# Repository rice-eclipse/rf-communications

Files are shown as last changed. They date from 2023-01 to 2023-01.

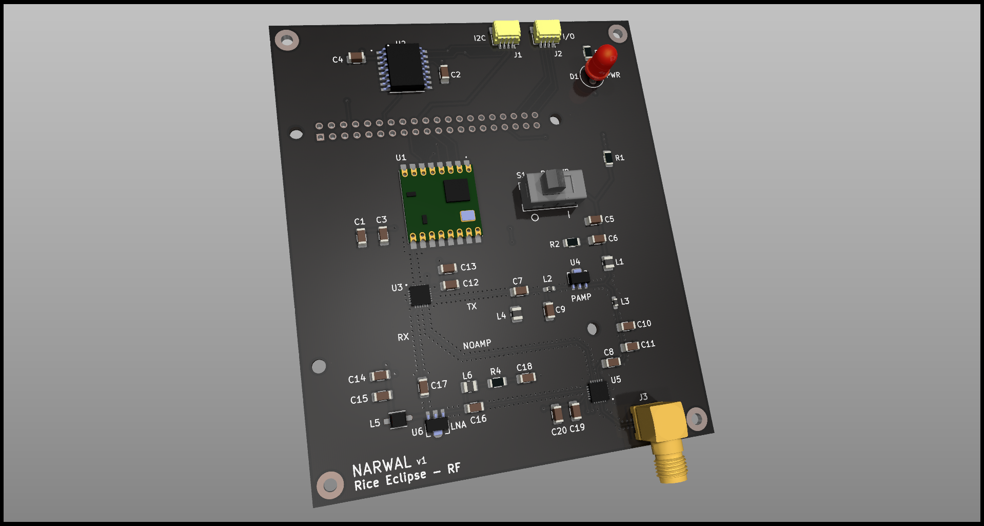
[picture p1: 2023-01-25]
narwal/Narwal_v1/Screenshots/Narwal_side_pop_ray.png

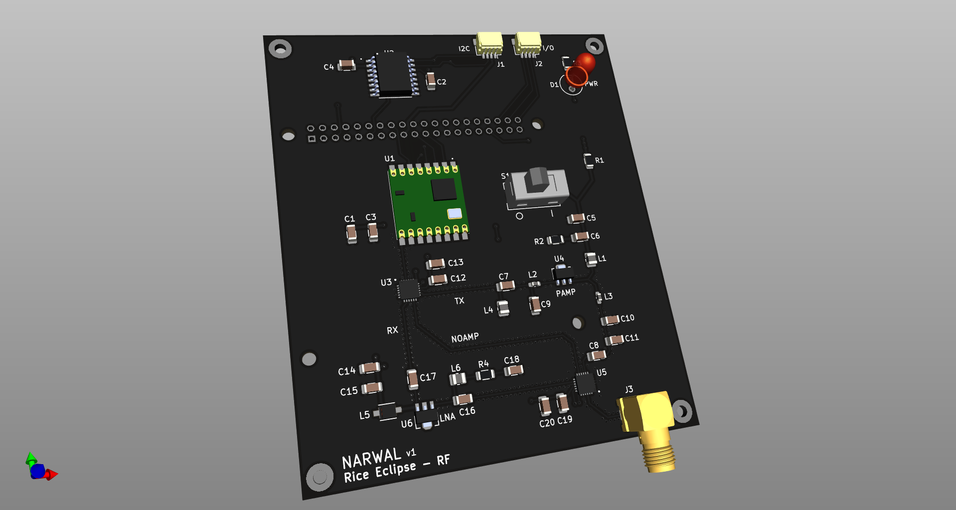
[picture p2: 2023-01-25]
narwal/Narwal_v1/Screenshots/Narwal_side_pop.png

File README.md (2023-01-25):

# RF Communications

This is the work completed by Rice Eclipse's RF Communications team.

RF Communications aims to build a long-range wireless communications system to interface with Real-Time-Rocket (RTR), Eclipse's custom flight instruments package, and receive telemetry data from RTR during flight.

The work completed by Eclipse's Flight Instruments team in developing RTR can be found [here](https://github.com/rice-eclipse/Real-Time-Rocket).

## NARWAL
NARWAL, or Long-range Amplified Wireless Radio for Aerial Navigation, is Eclipse's custom ground station PCB with radio communications capabilities.

NARWAL is designed to communicate with RTR from a range of at least 30,000 feet. While primarily intended to receive data, NARWAL is designed to be capable of both transmission and reception, and to amplify both transmitted and received signals.

NARWAL v1 was designed during the Fall 2022 semester, and will be assembled during the Spring 2023 semester. Eclipse plans to deploy NARWAL alongside [Unnamed Antenna] and RTR during the launch of Eclipse's Icarus & Daedalus rocket at the Spaceport America Cup in June 2023.

## [Unnamed Antenna]
During the Spring 2023 semester, RF Communications will design and construct a custom antenna to be used with NARWAL.

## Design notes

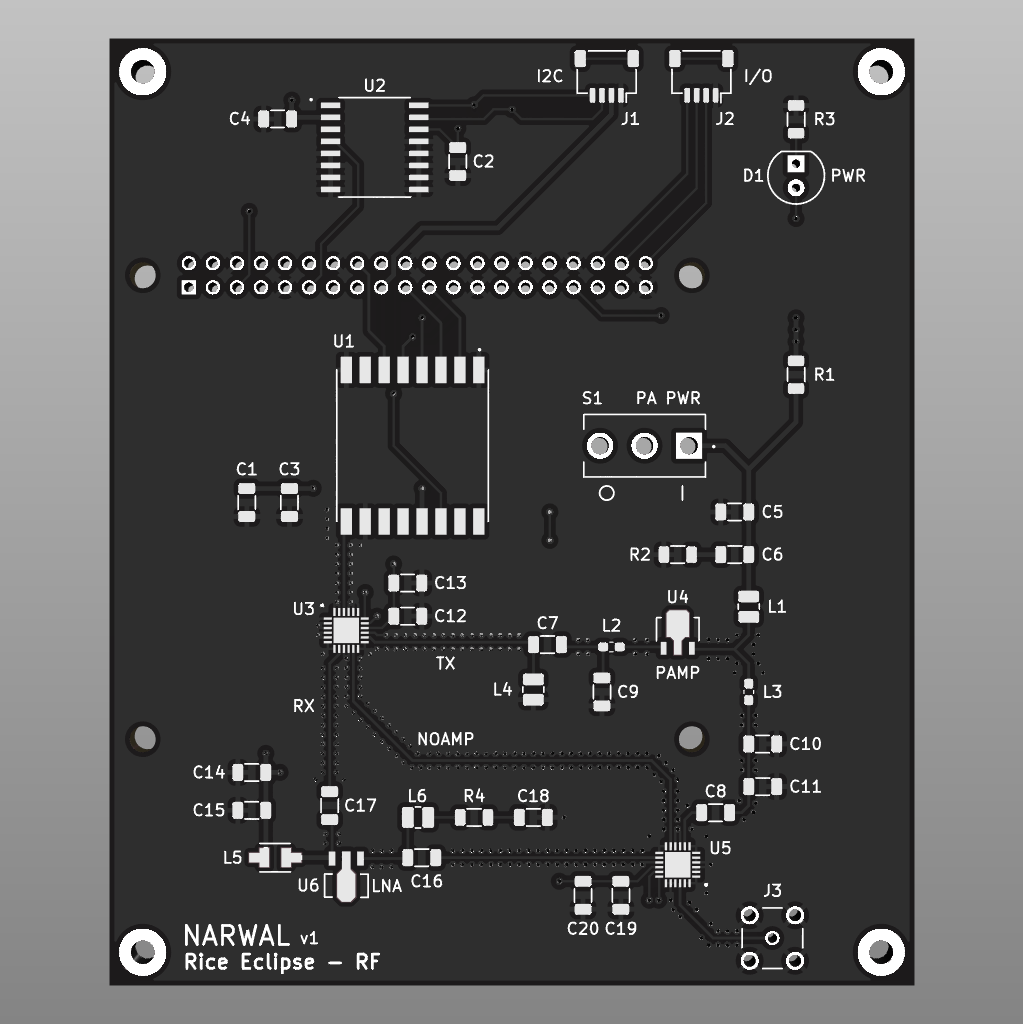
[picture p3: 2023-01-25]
narwal/Narwal_v1/Screenshots/Narwal_persp.png

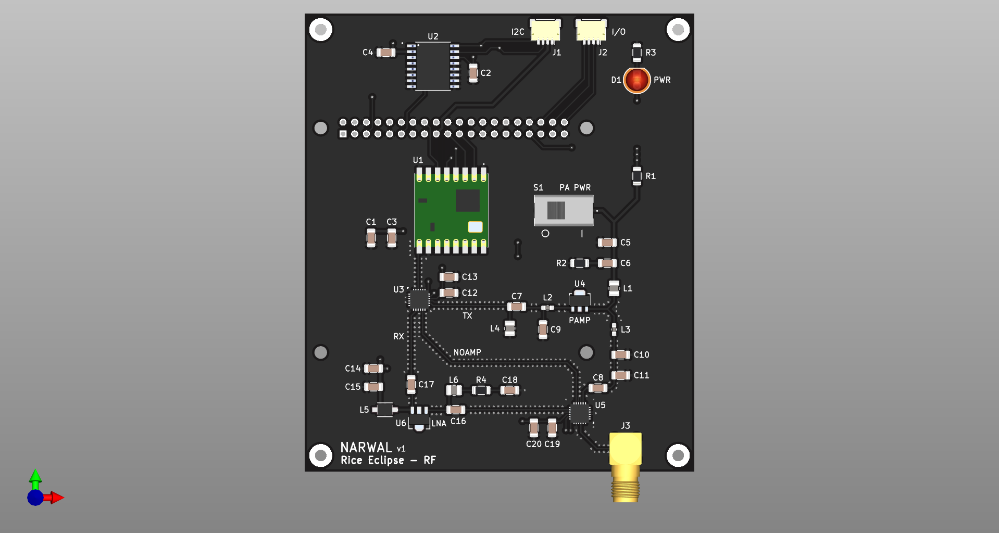
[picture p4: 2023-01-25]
narwal/Narwal_v1/Screenshots/Narwal_ortho_pop.png

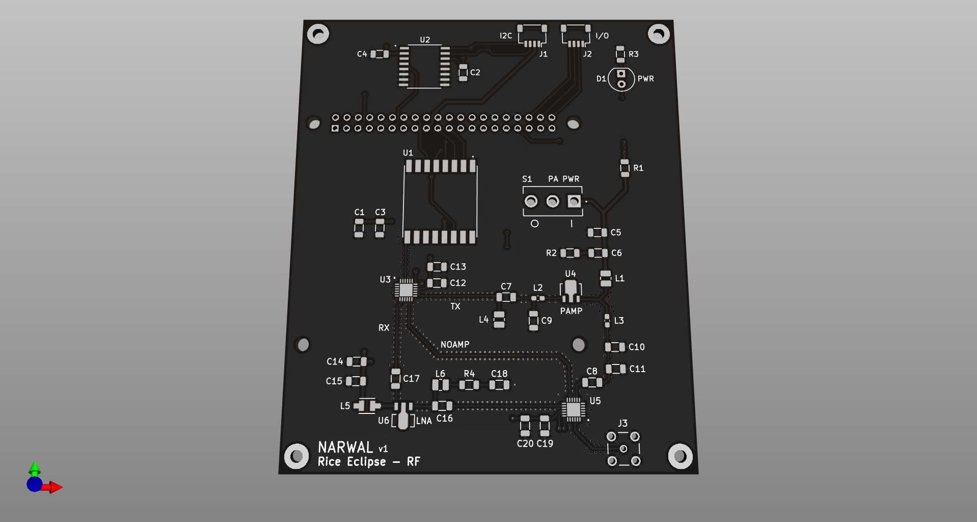
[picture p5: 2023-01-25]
narwal/Narwal_v1/Screenshots/Narwal_tilt.png

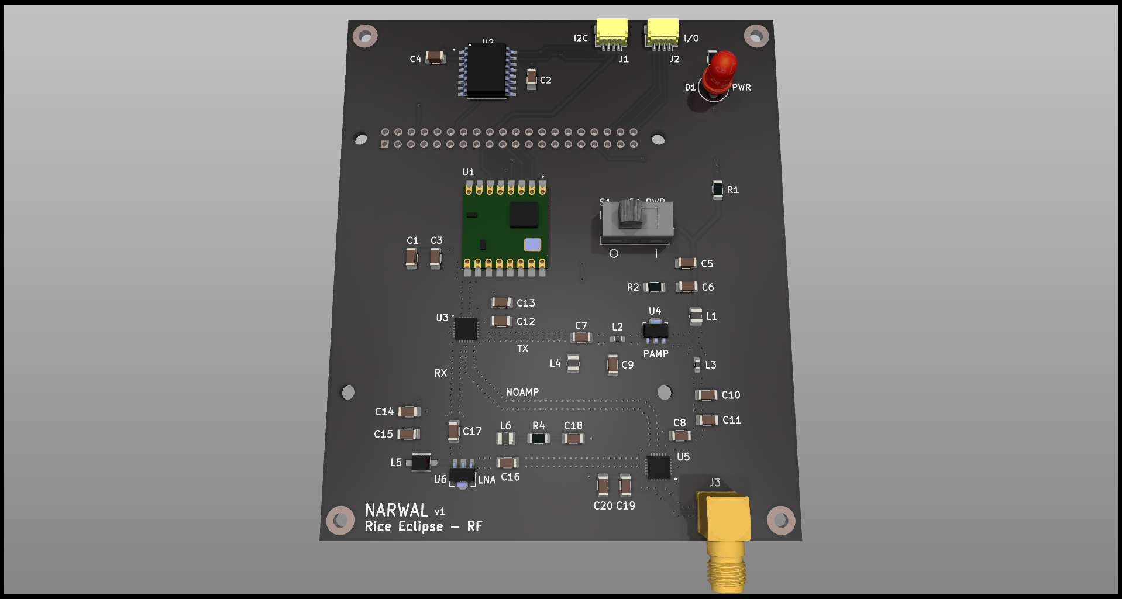
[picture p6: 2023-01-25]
narwal/Narwal_v1/Screenshots/Narwal_tilt_pop_ray.png

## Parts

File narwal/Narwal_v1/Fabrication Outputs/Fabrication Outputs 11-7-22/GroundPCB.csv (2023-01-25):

Id | Designator | Package | Quantity | Designation | Supplier and ref
1 | L1 | L_1008_2520Metric | 1 | 40n
2 | C5,C2 | C_1206_3216Metric | 2 | 0.01u
3 | R2 | R_1206_3216Metric | 1 | 5.1R
4 | L3 | L_1210_3225Metric | 1 | 4.3n
5 | R3,R4 | R_1206_3216Metric | 2 | 4.7K
6 | IC2,IC1 | SWITCH-HSWA4-63DR+ | 2 | SWITCH-HSWA4-63DR+
7 | C10,C11 | C_1206_3216Metric | 2 | 6.8p
8 | L4 | CHOKE-LQH44PN4R7MP0L | 1 | CHOKE-LQH44PN4R7MP0L
9 | L5 | L_1008_2520Metric | 1 | 47n
10 | A1 | RPI-4 | 1 | RPI-ZERO-ADA3708
11 | C16,C15,C9 | C_1206_3216Metric | 3 | 100p
12 | U1 | PAMP-HMC453ST89ETR | 1 | HMC452ST89ETR
13 | C18,C17 | C_1206_3216Metric | 2 | 1u
14 | C14 | C_1206_3216Metric | 1 | 0.1u
15 | C19,C20 | C_1206_3216Metric | 2 | 0.47u
16 | U4 | RTC-DS3231M-TRL | 1 | DS3231M
17 | C4 | C_1206_3216Metric | 1 | 330p
18 | C1 | C_1206_3216Metric | 1 | 12p
19 | C6,C13 | C_1206_3216Metric | 2 | 10u
20 | C8 | C_1206_3216Metric | 1 | 2.2u
21 | J1 | SMA-LPRS-CONNECTOR | 1 | SMA-LPRS-CONNECTOR
22 | R1 | R_1206_3216Metric | 1 | 150R
23 | D1 | LED_D3.0mm | 1 | LED
24 | U3 | TRX-RFM98W-433 | 1 | RFM96W-433S2
25 | L6 | L_1210_3225Metric | 1 | 5.1n
26 | C12 | C_1206_3216Metric | 1 | 39p
27 | R5 | R_1206_3216Metric | 1 | 154R
28 | BT1 | BATT-S8411-45R | 1 | BATT-S8411-45R
29 | L2 | L_1008_2520Metric | 1 | 620n
30 | C3 | C_1206_3216Metric | 1 | 15p
31 | C7 | C_1206_3216Metric | 1 | 0.33u
32 | U2 | LNA-PGA-103+ | 1 | PGA-103+

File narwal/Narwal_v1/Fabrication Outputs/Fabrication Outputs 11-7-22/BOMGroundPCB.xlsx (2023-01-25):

Comment | Designator | Footprint
40nH | L1 | 1008
620nH | L2 | 1008
4.3nH | L3 | 1210
47nH | L5 | 1008
5.1nH | L6 | 1210
12pF | C1 | 1206
0.01uF | C2, C5 | 1206
15pF | C3 | 1206
330pF | C4 | 1206
10uF | C6, C13 | 1206
0.33uF | C7 | 1206
2.2uF | C8 | 1206
100pF | C9, C15, C16 | 1206
6.8pF | C10, C11 | 1206
39pF | C12 | 1206
0.1uF | C14 | 1206
1uF | C17, C18 | 1206
0.47uF | C19, C20 | 1206
150R | R1 | 1206
5.1R | R2 | 1206
4.7K | R3, R4 | 1206
154R | R5 | 1206

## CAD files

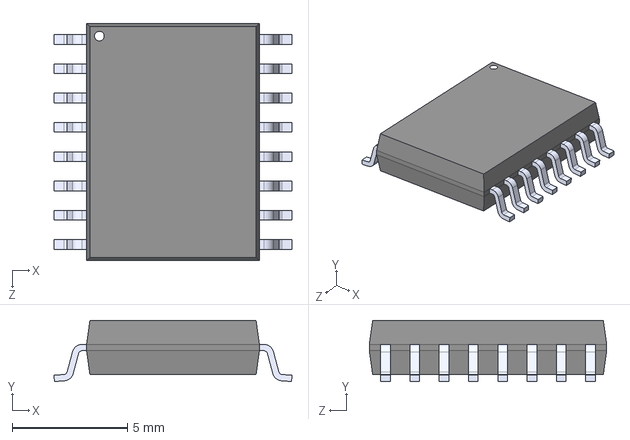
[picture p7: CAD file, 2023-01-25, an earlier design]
narwal/Eclipse_RF_Library/Old Libraries/DS3231M_TRL/DS3231M_TRL.step
10.3 x 2.65 x 10.3 mm

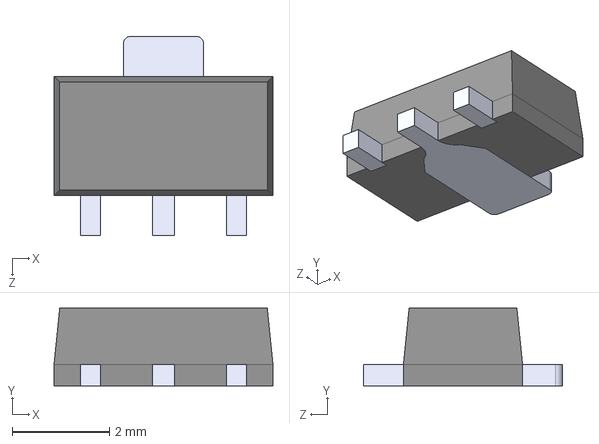
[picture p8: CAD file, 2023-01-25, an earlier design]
narwal/Eclipse_RF_Library/Old Libraries/IC_HMC311ST89E/IC_HMC311ST89E.step
4.50 x 1.60 x 4.10 mm

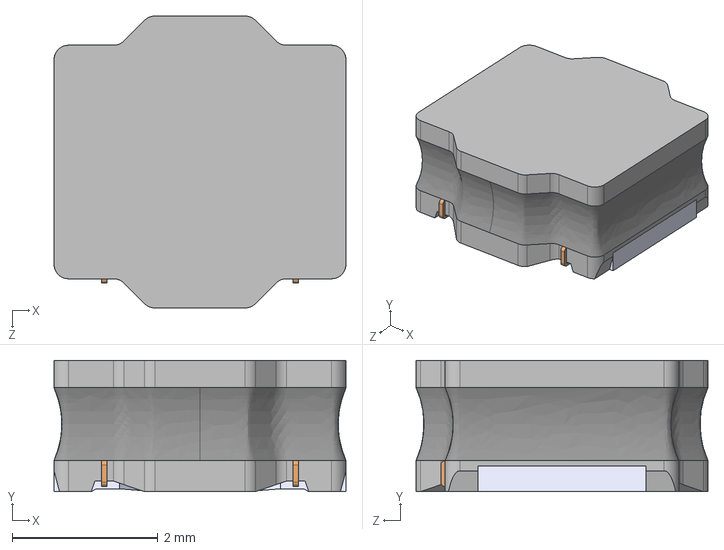
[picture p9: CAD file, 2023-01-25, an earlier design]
narwal/Eclipse_RF_Library/Old Libraries/LQH44PN4R7MP0L/LQH44PN4R7MP0L.step
4.00 x 1.80 x 4.00 mm

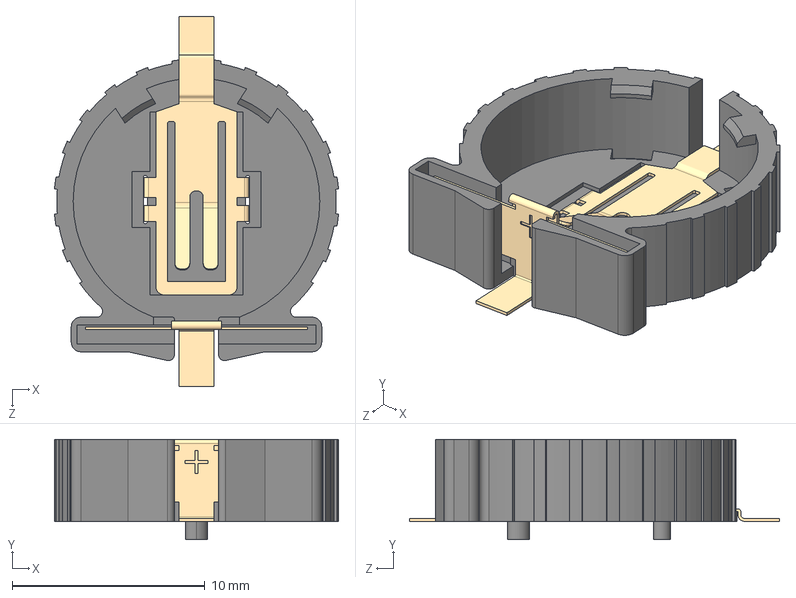
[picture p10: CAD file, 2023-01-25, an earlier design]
narwal/Eclipse_RF_Library/Old Libraries/S8411-45R--3DModel-STEP-56544 (1).STEP
14.7 x 5.20 x 19.2 mm

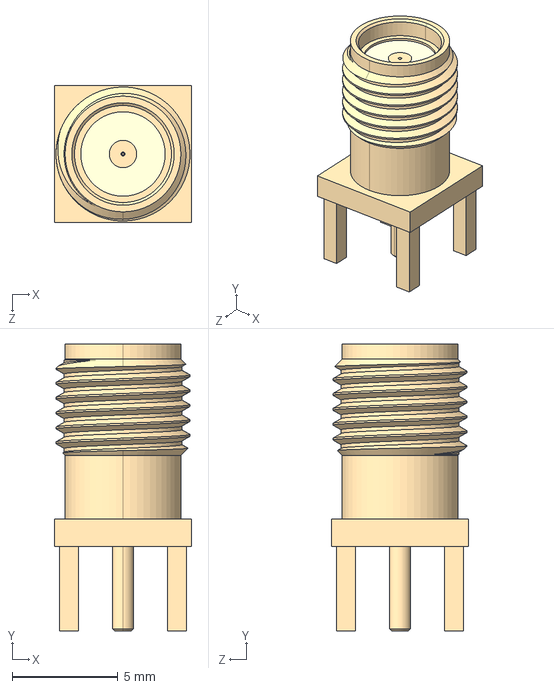
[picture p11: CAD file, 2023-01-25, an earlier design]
narwal/Eclipse_RF_Library/Old Libraries/SMA_CONNECTOR/SMA-LPRS-CONNECTOR-2.step
6.50 x 13.6 x 6.50 mm

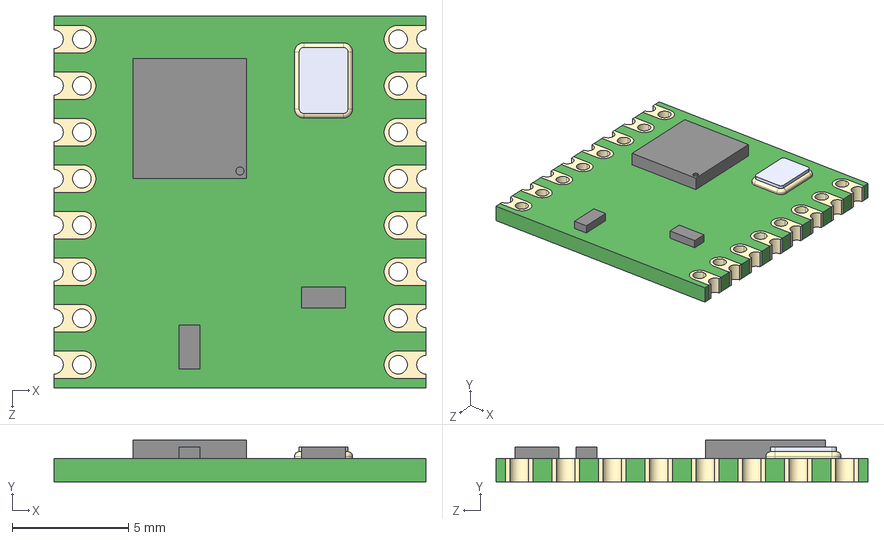
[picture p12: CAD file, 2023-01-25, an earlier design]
narwal/Eclipse_RF_Library/Old Libraries/Unusued Parts/RFM98W-433S2/RFM98W-433S2.step
16.0 x 1.80 x 16.0 mm

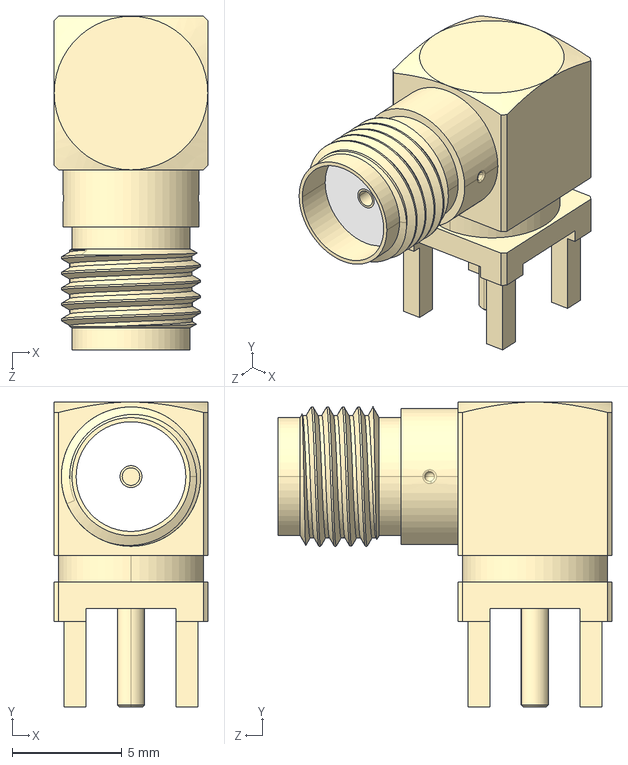
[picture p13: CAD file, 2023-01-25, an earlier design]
narwal/Eclipse_RF_Library/Old Libraries/SMA_CONNECTOR/SMA-LPRS-CONNECTOR.STEP
7.00 x 13.9 x 15.2 mm

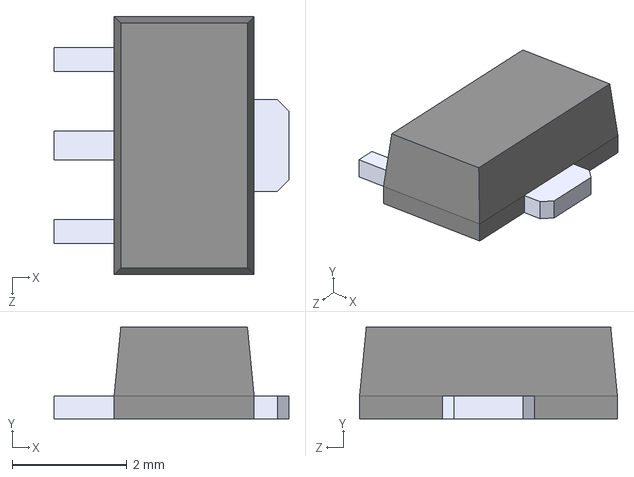
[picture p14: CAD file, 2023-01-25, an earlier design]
narwal/Eclipse_RF_Library/Old Libraries/TS78L05ACY RMG.STEP
4.10 x 1.60 x 4.50 mm

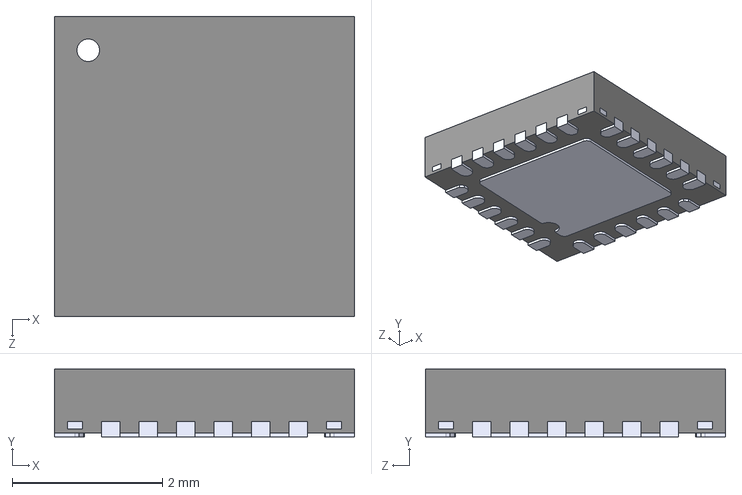
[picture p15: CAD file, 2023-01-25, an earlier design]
narwal/Eclipse_RF_Library/Old Libraries/ATSAMD10D13A-MNT.STEP
4.00 x 0.9 x 4.00 mm

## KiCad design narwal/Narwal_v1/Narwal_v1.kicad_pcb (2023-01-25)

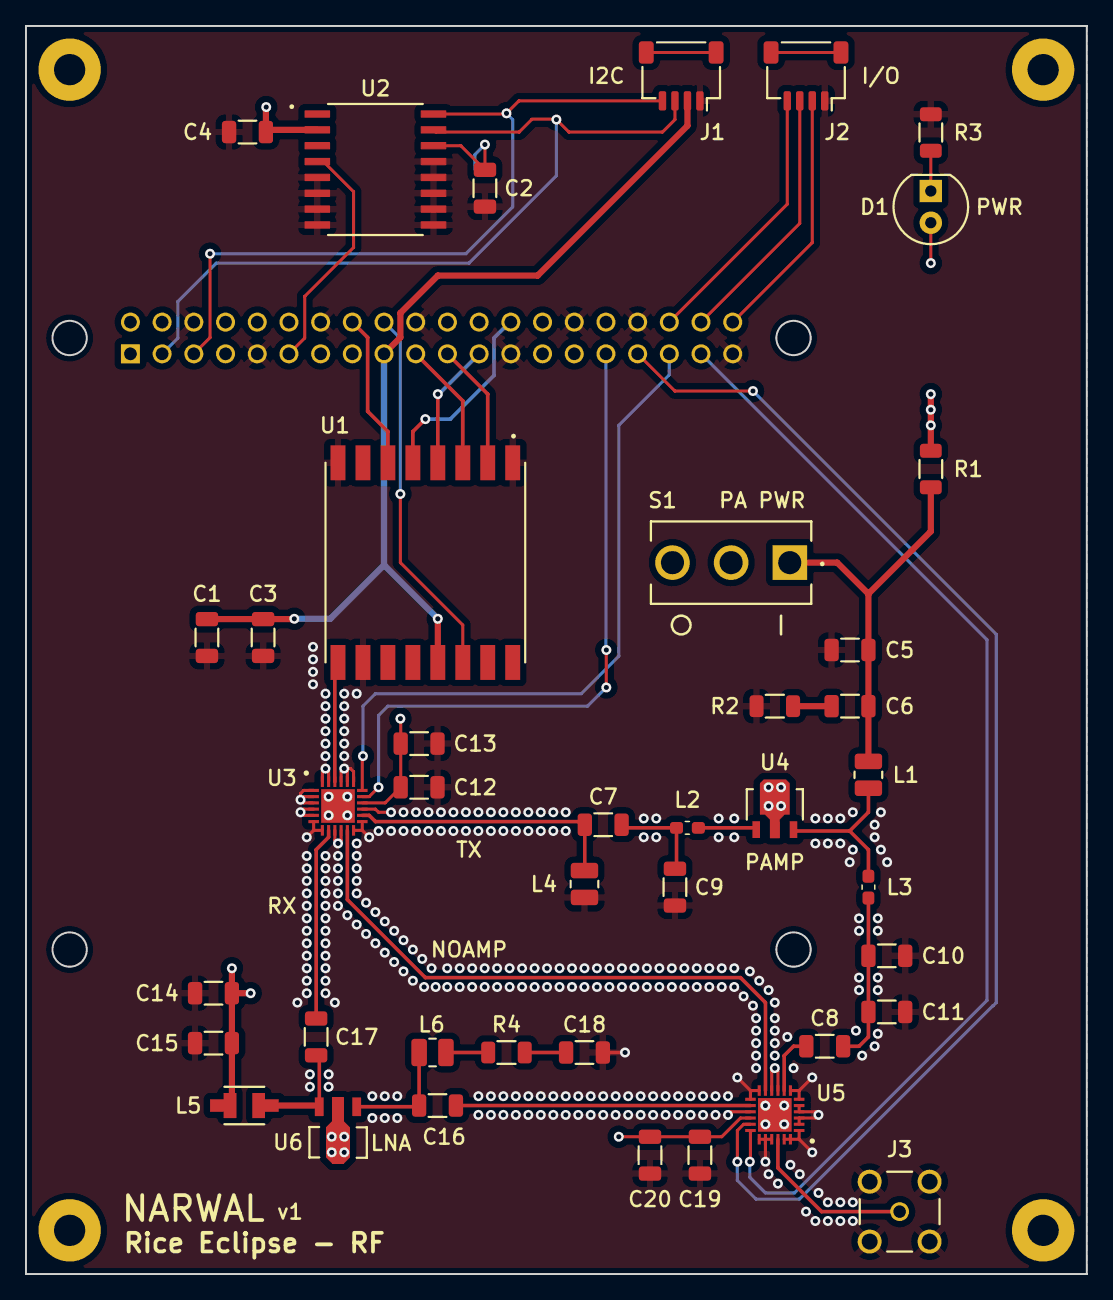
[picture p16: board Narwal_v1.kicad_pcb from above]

Board: 4 copper layers, 85.0 x 100.0 mm, 47 parts (1 on the bottom side), 38 nets.

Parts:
A1: RASPBERRY-PI; RPI-4
BT1: S8411-45R; BATT-S8411-45R
C1, C13, C20: 1u; C_1206_3216Metric
C2, C3, C4: 100n; C_1206_3216Metric
C5: 2.2u; C_1206_3216Metric
C6, C12, C19: 100p; C_1206_3216Metric
C7: 12p; C_1206_3216Metric
C8: 39p; C_1206_3216Metric
C9: 15p; C_1206_3216Metric
C10, C11: 6.8p; C_1206_3216Metric
C14: 10u; C_1206_3216Metric
C15: 330n; C_1206_3216Metric
C16, C17: 10n; C_1206_3216Metric
C18: 330p; C_1206_3216Metric
D1: PWR; LED_D5.0mm
H1, H2, H3, H4: MountingHole_Pad; MountingHole_2.5mm_Pad
J1, J2: JST-SH; JST_SH_SM04B-SRSS-TB_1x04-1MP_P1.00mm_Horizontal
J3: SMA-LPRS; SMA-LPRS-CONNECTOR
L1: 47n; L_1008_2520Metric
L2: 4.3n; L_0603_1608Metric_Pad1.05x0.95mm_HandSolder
L3: 5.1n; L_0603_1608Metric_Pad1.05x0.95mm_HandSolder
L4: 40n; L_1008_2520Metric
L5: LQH32NH4R7J23L; CHOKE-LQH32NH4R7J23L
L6: 620n; L_1008_2520Metric
R1: 0R; R_1206_3216Metric
R2: 5.1R; R_1206_3216Metric
R3: 1K; R_1206_3216Metric
R4: 150R; R_1206_3216Metric
S1: 500SSP1S1M2QEA; SWITCH-500SSP1S1M2QEA
U1: RFM96W-433; TRX-RFM98W-433
U2: DS3231M; RTC-DS3231M-TRL
U3, U5: HSWA4-63DR+; SWITCH-HSWA4-63DR+
U4: HMC452ST89; PAMP-HMC453ST89ETR
U6: PGA-103+; LNA-PGA-103+

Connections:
+3.3V: A1.17 (3V3[2]), C1.2, C3.2, J1.2, U1.13 (3.3V)
+5V: A1.2 (5V[1]), A1.4 (5V[2]), C4.2, C12.1, C13.1, C14.1, C15.1, C19.1, C20.1, D1.2 (A), L5.1, R1.1, S1.2, U2.2 (VCC), U3.16 (VDD), U5.16 (VDD)
BUT1: A1.36 (GPIO16), J2.4
BUT2: A1.38 (GPIO20), J2.3
BUT3: A1.40 (GPIO21), J2.2
CS: A1.26 (~CE1/GPIO7), U1.5 (NSS)
CTRL1A: A1.31 (GPIO6), U3.17 (CONTROL_1)
CTRL1B: A1.33 (GPIO13), U5.17 (CONTROL_1)
CTRL2A: A1.35 (GPIO19), U3.18 (CONTROL_2)
CTRL2B: A1.37 (GPIO26), U5.18 (CONTROL_2)
DIO0: A1.18 (GEN5/GPIO24), U1.14 (DIO0)
GND: A1.6 (GND[8]), A1.9 (GND[1]), A1.14 (GND[4]), A1.20 (GND[5]), A1.25 (GND[2]), A1.30 (GND[6]), A1.34 (GND[7]), A1.39 (GND[3]), BT1.N, C1.1, C2.2, C3.1, C4.1, C5.2, C9.2, C10.2, C11.2, C12.2, C13.2, C14.2, C15.2, C18.2, C19.2, C20.2, J1.1, J2.1, J3.G1, J3.G2, J3.G3, J3.G4, L4.2, R2.2, R3.2, U1.1 (GND), U1.8 (GND), U1.10 (GND), U2.5 (GND), U2.6 (GND), U2.7 (GND), U2.8 (GND), U2.9 (GND), U2.10 (GND), U2.11 (GND), U2.12 (GND), U2.13 (GND), U3.1 (GND_1), U3.2 (GND_2), U3.3 (GND_3), U3.4 (GND_4), U3.5 (RF4), U3.6 (GND_5), U3.7 (GND_6), U3.9 (GND_7), U3.10 (GND_8), U3.12 (GND_9), U3.13 (GND_10), U3.15 (GND_11), U3.19 (CONTROL_3), U3.20 (GND_12), U3.21 (GND_13), U3.23 (GND_14), U3.24 (GND_15), U3.25 (PADDLE), U4.2 (GND), U5.1 (GND_1), U5.2 (GND_2), U5.3 (GND_3), U5.4 (GND_4), U5.5 (RF4), U5.6 (GND_5), U5.7 (GND_6), U5.9 (GND_7), U5.10 (GND_8), U5.12 (GND_9), U5.13 (GND_10), U5.15 (GND_11), U5.19 (CONTROL_3), U5.20 (GND_12), U5.21 (GND_13), U5.23 (GND_14), U5.24 (GND_15), U5.25 (PADDLE), U6.2 (GND)
LNA-ANT: C16.1, U5.14 (RF1)
LNA-TRX: C17.2, U3.8 (RF3)
MISO: A1.21 (GPIO9/MISO), U1.2 (MISO)
MOSI: A1.19 (GPIO10/MOSI), U1.3 (MOSI)
NOAMP: U3.11 (RF2), U5.11 (RF2)
unnamed: BT1.P, C2.1, U2.14 (VBAT)
unnamed: C5.1, C6.1, L1.1, R1.2, S1.1
unnamed: C6.2, R2.1
unnamed: C7.2, C9.1, L2.1
unnamed: C8.1, C10.1, C11.1, L3.2
unnamed: C16.2, L6.1, U6.1
unnamed: C17.1, L5.2, U6.3
unnamed: C18.1, R4.2
unnamed: D1.1 (K), R3.1
unnamed: J3.1, U5.22 (RF_COM)
unnamed: L1.2, L3.1, U4.3
unnamed: L2.2, U4.1
unnamed: L6.2, R4.1
PAMP-ANT: C8.2, U5.8 (RF3)
PAMP-TRX: C7.1, L4.1, U3.14 (RF1)
RST-RTC: A1.11 (GPIO17/GEN0), U2.4 (~RST)
RST-TRX: A1.16 (GEN4/GPIO23), U1.6 (RESET)
SCL: A1.5 (GPIO3/SCL), J1.4, U2.16 (SCL)
SCLK: A1.23 (GPIO11/SCLK), U1.4 (SCK)
SDA: A1.3 (GPIO2/SDA), J1.3, U2.15 (SDA)
TRX: U1.9 (ANT), U3.22 (RF_COM)

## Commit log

2022-09-07 create Code and PCBs folders
2022-09-15 This is a Pi Zero W schematic&&footprint commit
2022-09-15 This is a 2nd Pi Zero W schematic&&footprint commit
2022-09-18 added RFM98W transceiver symbol & footprint
2022-09-22 created pcb file
    [GroundStationBoard.kicad_pcb, GroundStationBoard.kicad_sch, RFM98W-433S2.step]
2022-09-22 added footprint for switch
2022-09-22 4 layer-ifying the PCB, traces, board cuts and trace width
    [GroundStationBoard.kicad_pcb, GroundStationBoard.kicad_sch]
2022-09-27 added SMA connector and RF switch to schematic
    [GroundStationBoard.kicad_pcb, GroundStationBoard.kicad_sch, SMA_CONNECTOR.step]
2022-09-27 worked on data I/O pins
    [GroundStationBoard.kicad_pcb, GroundStationBoard.kicad_sch]
2022-09-29 added amplifier
    [GroundStationBoard.kicad_pcb, GroundStationBoard.kicad_sch]
2022-09-29 decoupling capacitors & amplifier
    [GroundStationBoard.kicad_sch]
2022-10-23 Current code from Carter
2022-10-27 Test cases now sends bursts of 10 packets per case, to ensure reception. Added a number of comments and helpful messages for future reference.
2022-11-07 pre-revision backup
    [ATSAMD10D13A-MNT.STEP, BOMGroundPCB.xlsx, CONSMA002-G--3DModel-STEP-56544.STEP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]
2022-11-08 connectors, switch, test points
    [GroundPCB.kicad_sch]
2022-11-10 Began working on data visualization and created temporary dummy log.tsv for testing
    [log.tsv]
2022-11-14 initial layout changes
    [GroundPCB.kicad_pcb, GroundPCB.kicad_sch]
2022-11-14 relocated components, added switch to layout
    [GroundPCB.kicad_pcb, GroundPCB.kicad_sch]
2022-11-14 data_grapher.py should now work as intended. We'll see if we get any issues once we actually have data to graph!
    [log.tsv]
2022-11-21 post-review revisions
    [BOMGroundPCB.xlsx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]
2022-11-21 name change and readme
    [BOMGroundPCB.xlsx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]
2022-12-08 power switch fixes, JLC compatibility changes
    [GroundPCB-B_Cu.gbr, GroundPCB-B_Silkscreen.gbr, GroundPCB-Edge_Cuts.gbr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]
2022-12-08 JLC-required silkscreen changes
    [BOMGroundPCB.xlsx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]
2022-12-13 final changes and fabrication
    [GroundStationBoard.kicad_pcb, GroundStationBoard.kicad_sch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]
2023-01-13 Ensuring github is all up-to-date
    [log.tsv]
2023-01-13 Radio *does* need to create SPI in init though
2023-01-18 transmissionTestSend.py and transmissionTestReceive.py now print the radio configuration
2023-01-18 Send now prints ack_pack
2023-01-18 Send and Receive now print the packet (or None) that they've received
2023-01-18 Added plenty of debug prints
2023-01-18 Debug print
2023-01-20 print update
2023-01-22 test commit
    [log.tsv]
2023-01-22 Log file (log.yaml now) is updated immediately after each test, so data will not be lost in the event of a fatal error
    [log.tsv]
2023-01-22 print changes
